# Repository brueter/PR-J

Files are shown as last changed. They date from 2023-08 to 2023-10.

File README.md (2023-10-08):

<p align="center">
    <picture>
        <source media="(prefers-color-scheme: dark)" srcset="./images/dark.svg" | width=300>
        <source media="(prefers-color-scheme: light)" srcset="./images/light.svg" | width=300>
        sammich
    </picture>
</p>

## PR and what now?
PR&J is the second name of this project after realizing two things:
- I'd like to be able to put this on a resume.
- Realizing the main features are as follows:
    - Probing
    - Runout detection
    - & Jam detection
> This board also is sandwiched between the hotend and extruder, thus a PR&J.

> If you'd like to know the first name of the board scroll up a bit in the discord

## How does a load cell do all that?
The way this design is set to work is there will be a strain gauge between the extruder and hotend with a set of resistors on it.
When the board experiences even the slightest bit of strain, the value of these resistors changes slightly.
This change is amplified by the tried and true HX717 24 bit amplifier, allowing for over 16 million unique values.
This signal is then read by an on board ATTiny202, and then sent to a klipper MCU via I<sub>2</sub>C.

Though the first idea that comes to mind with load cells is probing (which is still the main feature of this project), the ability to detect this strain can also be used to interpret forces between the hotend and extruder in both positive and negative directions.
We're still workshopping ideas that could come from this one feature, but some we would like to consider are:
- Runout detection
- Jam detection
- Detecting skipped steps
- One-click pressure advance tuning
- One-click max flow rate calculation

Some "theoreticals" that will need extensive testing but may be possible:
- Spaghetti detection
- Crash detection
- Flow rate change compensation

## Sign me up!
Actually I'd love to!
We're in the process of establishing a small beta test group for main boards and two types of strain gauges. The initial testing phase likely won't involve much printing, focusing instead on gathering data to study the behavior of these strain gauges, as well as test consistency.
As we develop more, the strain gauges we currently have may be adapted to some toolheads, so it's likely that new hardware won't even have to be sent for real world testing.
We're also looking for people that may have experience with any of the following for helping with development of the project itself.
- Skilled programmers, especially those familiar with klipper
- Electronics engineers
- CAD experts
If you're interested in contributing, ongoing discussions are hosted on the [Armchair Engineering discord server](https://discord.gg/armchairengineeringsux) in [this specific channel](https://discord.com/channels/1029426383614648421/1141480604844703745).

## What now?
As of the repository's creation, parts are on the way, and the board ordering process is nearly finalized. The initial batch of test boards will comprise approximately 10 main boards and 20 strain gauges (10 of each design).
Regular updates will be posted in the Armchair engineering project thread. Feel free to reach out to me there or through [my discord](https://discord.com/users/96435324275658752) if you have any questions.

Here's what we've got so far :)

<picture>
  <source srcset="./images/boards.png">
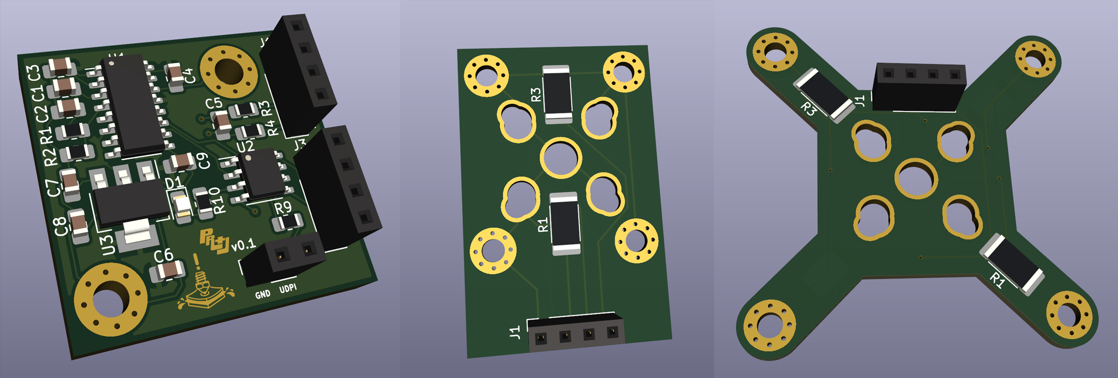
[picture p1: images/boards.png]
sammich
  
</picture>

## Helpers
- Electronics
    - [fisheiyy](https://github.com/fisheiyy)
    - [tanaes](https://github.com/tanaes)
    - [calithameridi](http://github.com/calithameridi/)
- Hardware
    - [tanaes](https://github.com/tanaes)
    - [bwnance](https://github.com/bwnance)
- Software
    - [detunedcalliope](https://github.com/detunedcalliope)

## Legal

Shield: [][cc-by-nc-sa]

This work is licensed under a
[Creative Commons Attribution-NonCommercial-ShareAlike 4.0 International License][cc-by-nc-sa].

[][cc-by-nc-sa]

[cc-by-nc-sa]: http://creativecommons.org/licenses/by-nc-sa/4.0/
[cc-by-nc-sa-image]: https://licensebuttons.net/l/by-nc-sa/4.0/88x31.png
[cc-by-nc-sa-shield]: https://img.shields.io/badge/License-CC%20BY--NC--SA%204.0-lightgrey.svg

FOR COMMERCIAL RIGHTS CONTACT AT brueter918@gmail.com

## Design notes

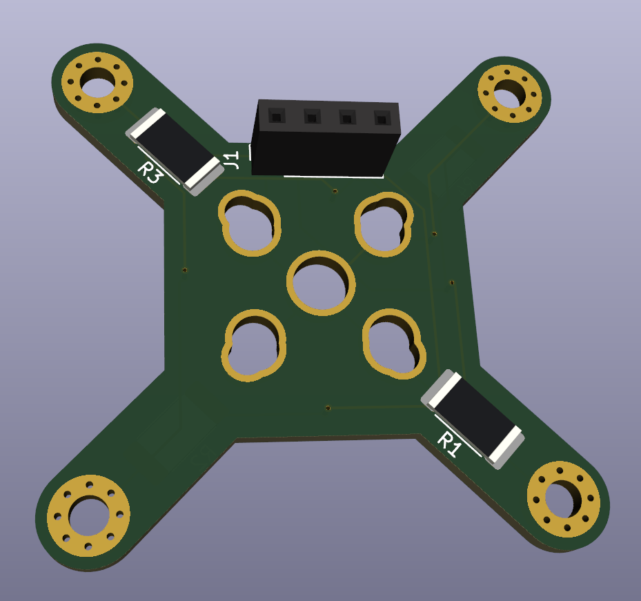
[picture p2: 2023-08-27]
images/square strain gauge.png

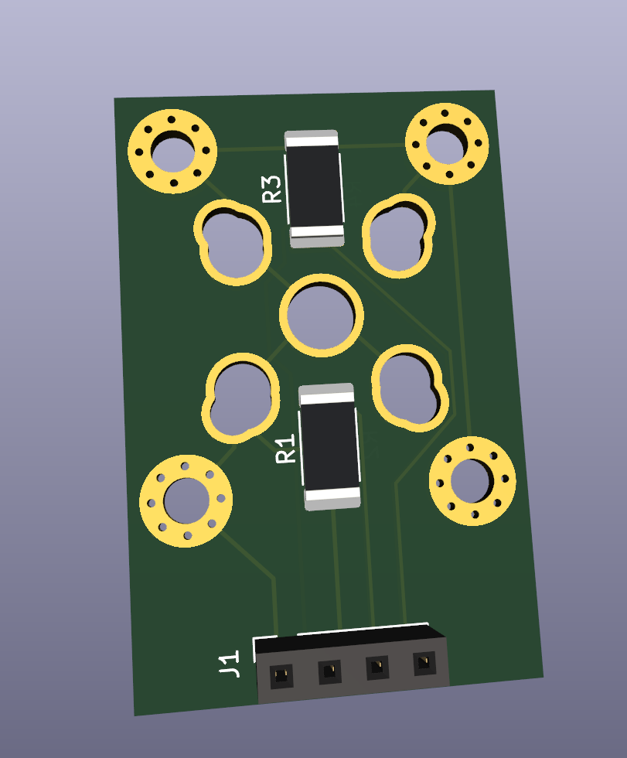
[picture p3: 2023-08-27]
images/minimal strain gauge.png

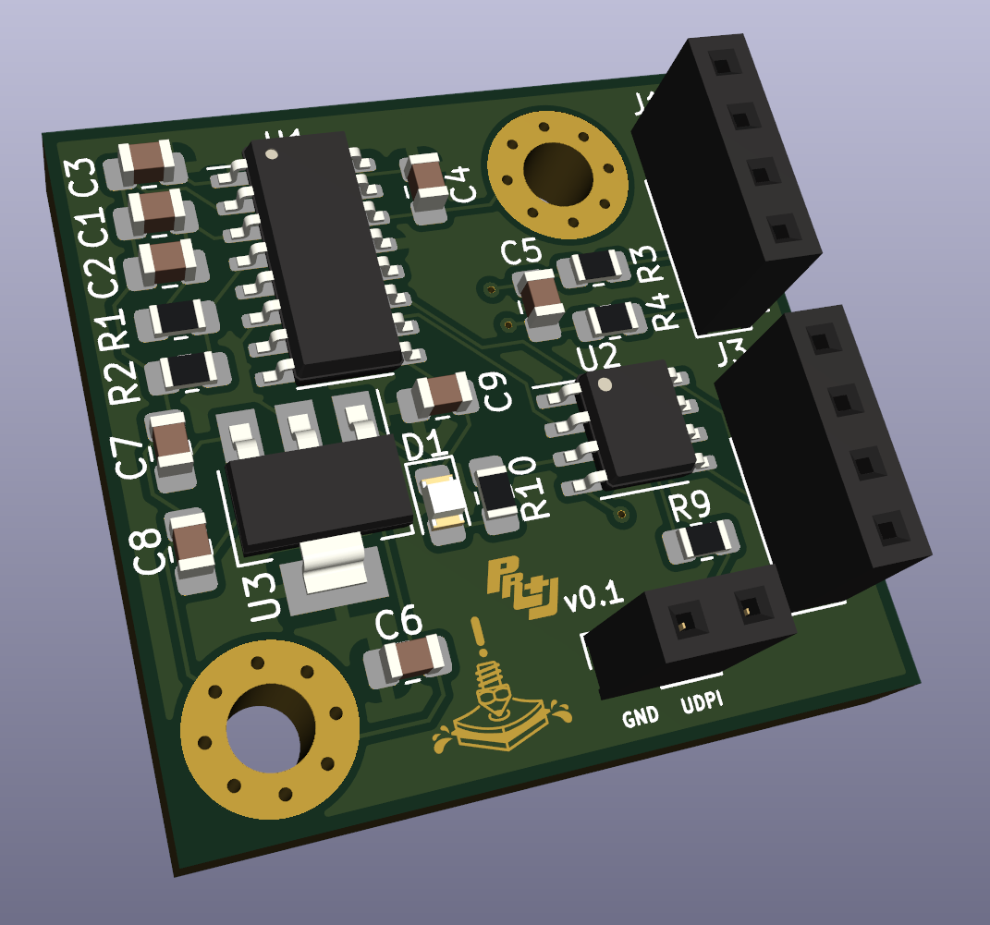
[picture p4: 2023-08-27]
images/driver board.png

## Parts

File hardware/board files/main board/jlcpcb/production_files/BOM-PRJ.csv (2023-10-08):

Comment | Designator | Footprint | LCSC
100 | R3 | R_0805_2012Metric_Pad1.20x1.40mm_HandSolder
10u | C7 | C_0805_2012Metric_Pad1.18x1.45mm_HandSolder
Strain Gauge | J1 | PinSocket_1x04_P2.54mm_Vertical
4k7 | R9 | R_0805_2012Metric_Pad1.20x1.40mm_HandSolder
MountingHole_Pad | H1 | MountingHole_3.2mm_M3_Pad_Via
12K | R2 | R_0805_2012Metric_Pad1.20x1.40mm_HandSolder
10u | C4 | C_0805_2012Metric_Pad1.18x1.45mm_HandSolder
HX717 | U1 | SOP-16_3.9x9.9mm_P1.27mm
10u | C9 | C_0805_2012Metric_Pad1.18x1.45mm_HandSolder
10u | C2 | C_0805_2012Metric_Pad1.18x1.45mm_HandSolder
Programmer | J2 | PinSocket_1x02_P2.54mm_Vertical
AMS1117-3.3 | U3 | SOT-223-3_TabPin2
ATtiny202-SS | U2 | SOIC-8_3.9x4.9mm_P1.27mm
KLIPPER | J3 | PinSocket_1x04_P2.54mm_Vertical
0u1 | C3 | C_0805_2012Metric_Pad1.18x1.45mm_HandSolder
100 | R4 | R_0805_2012Metric_Pad1.20x1.40mm_HandSolder
MountingHole_Pad | H2 | MountingHole_3.2mm_M3_Pad_Via
10u | C8 | C_0805_2012Metric_Pad1.18x1.45mm_HandSolder
0u1 | C5 | C_0805_2012Metric_Pad1.18x1.45mm_HandSolder
0u1 | C1 | C_0805_2012Metric_Pad1.18x1.45mm_HandSolder
100 | R10 | R_0805_2012Metric_Pad1.20x1.40mm_HandSolder
B1701NB | D1 | LED_0805_2012Metric_Pad1.15x1.40mm_HandSolder
0u1 | C6 | C_0805_2012Metric_Pad1.18x1.45mm_HandSolder
33K | R1 | R_0805_2012Metric_Pad1.20x1.40mm_HandSolder

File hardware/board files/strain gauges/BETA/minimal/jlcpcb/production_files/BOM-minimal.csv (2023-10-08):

Comment | Designator | Footprint | LCSC
PR&J | J1 | PinSocket_1x04_P2.54mm_Vertical
1k | R3 | R_2512_6332Metric
MountingHole_Pad | H1 | MountingHole_3.2mm_M3_Pad_Via
~ | U1 | hotend mounting holes
MountingHole_Pad | H2 | MountingHole_3.2mm_M3_Pad_Via
1k | R1 | R_2512_6332Metric
MountingHole_Pad | H3 | MountingHole_3.2mm_M3_Pad_Via
MountingHole_Pad | H4 | MountingHole_3.2mm_M3_Pad_Via
1k | R2 | R_2512_6332Metric
1k | R4 | R_2512_6332Metric

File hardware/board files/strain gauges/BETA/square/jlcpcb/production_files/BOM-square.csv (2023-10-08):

Comment | Designator | Footprint | LCSC
1k | R3 | R_2512_6332Metric_Pad1.40x3.35mm_HandSolder
1k | R1 | R_2512_6332Metric_Pad1.40x3.35mm_HandSolder
1k | R2 | R_2512_6332Metric_Pad1.40x3.35mm_HandSolder
1k | R4 | R_2512_6332Metric_Pad1.40x3.35mm_HandSolder

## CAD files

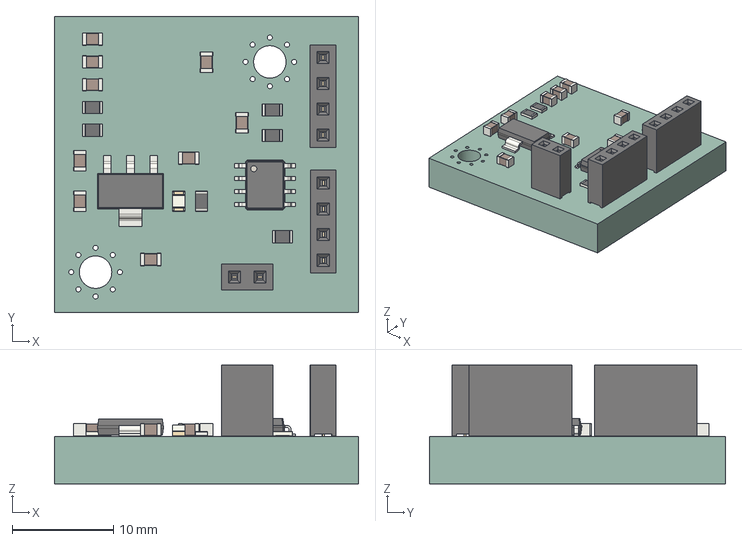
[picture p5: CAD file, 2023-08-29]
hardware/board files/main board/PRJ.step
30.0 x 29.2 x 11.7 mm
PRJ PCB

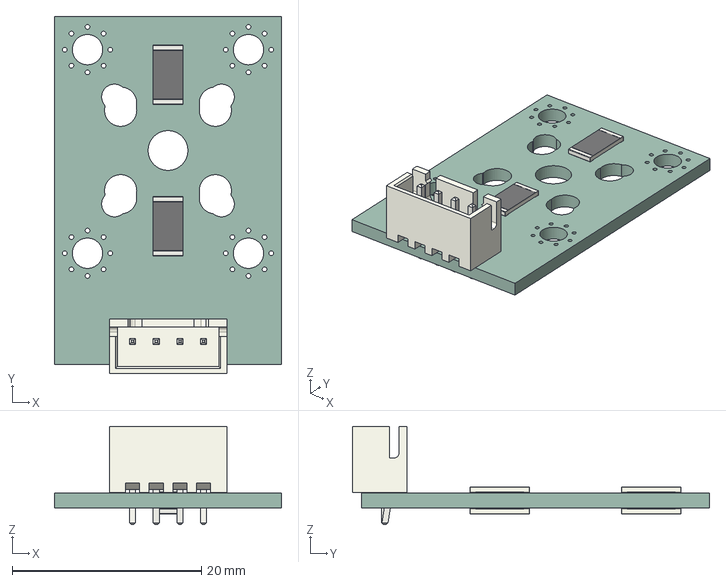
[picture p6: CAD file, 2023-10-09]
hardware/board files/strain gauges/BETA/minimal/strain gauge.step
24.0 x 37.7 x 10.4 mm
minimal PCB

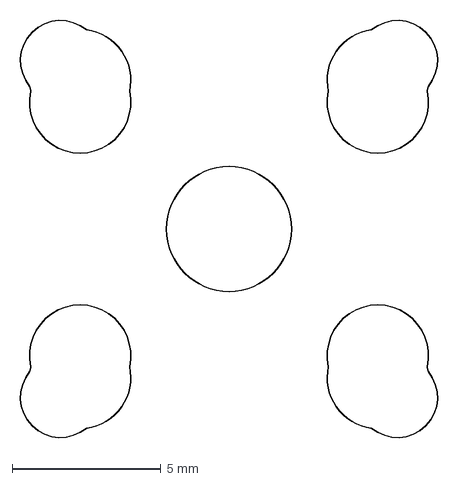
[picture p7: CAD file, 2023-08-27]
hardware/board files/strain gauges/hotend mounting holes.dxf
14.3 x 14.3 mm

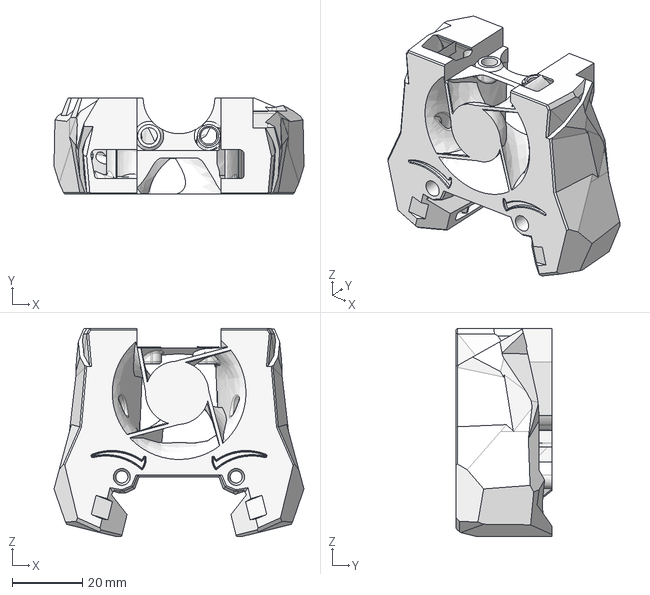
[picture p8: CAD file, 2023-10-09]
hardware/toolhead/cad/stealthjelly front.step
71.1 x 27.4 x 59.1 mm

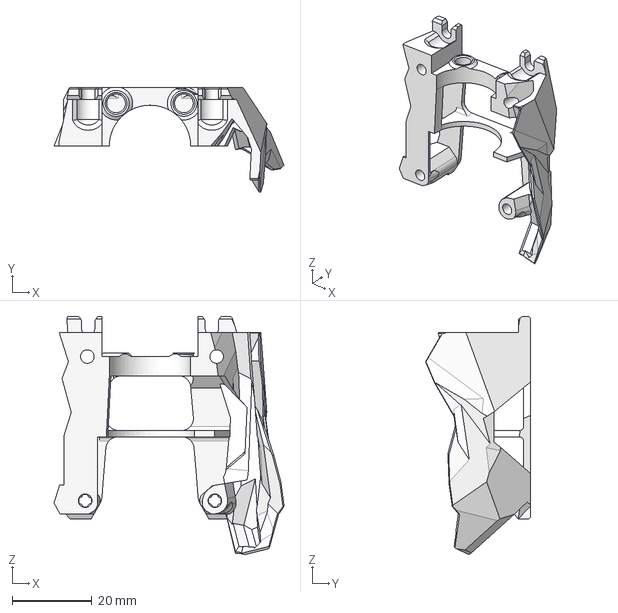
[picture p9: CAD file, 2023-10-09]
hardware/toolhead/cad/stealthjelly back.step
57.7 x 26.3 x 59.7 mm

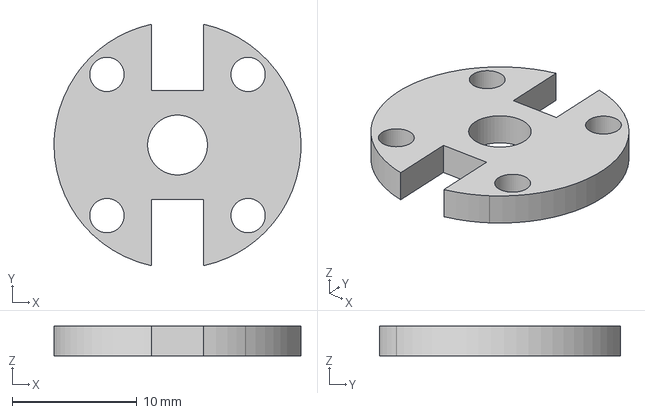
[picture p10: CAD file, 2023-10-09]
hardware/toolhead/cad/spacer.step
19.8 x 19.3 x 2.40 mm

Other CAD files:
hardware/toolhead/stl/spacer.stl
hardware/toolhead/stl/stealthjelly back.stl

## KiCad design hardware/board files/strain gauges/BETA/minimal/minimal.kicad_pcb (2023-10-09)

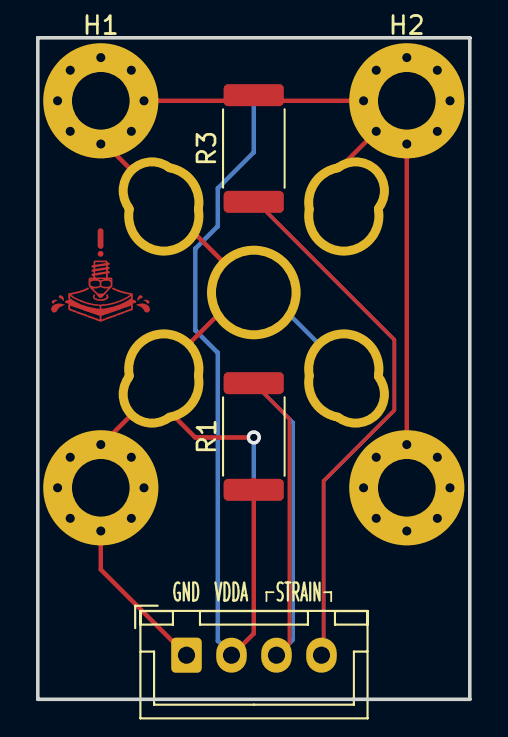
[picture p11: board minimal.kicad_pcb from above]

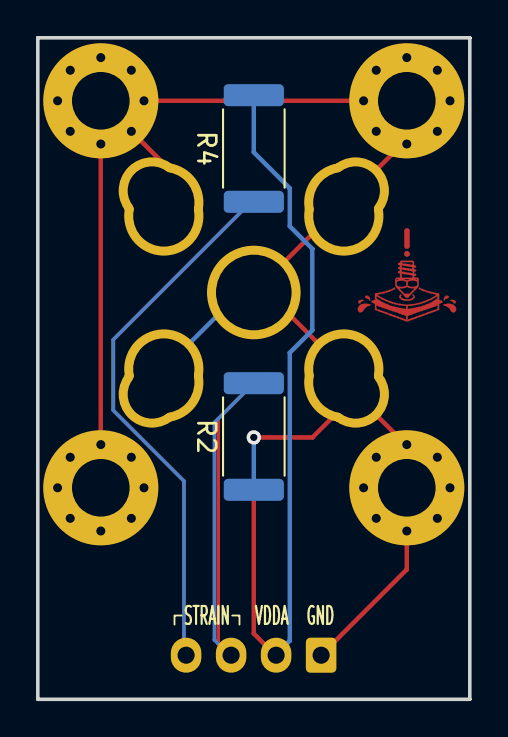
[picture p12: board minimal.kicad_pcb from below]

Board: 2 copper layers, 24.0 x 36.8 mm, 10 parts (2 on the bottom side), 4 nets.

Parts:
H1, H2, H3, H4: MountingHole_Pad; MountingHole_3.2mm_M3_Pad_Via
J1: PR&J; JST_XH_B4B-XH-A_1x04_P2.50mm_Vertical
R1, R2, R3, R4: 1k; R_2512_6332Metric
U1: hotend mounting holes

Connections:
GND: H1.1, H2.1, H3.1, H4.1, J1.1, R2.1, R3.2, U1.1 (GND)
IN+: J1.3, R1.2, R2.2
IN-: J1.4, R3.1, R4.1
VDDA: J1.2, R1.1, R4.2

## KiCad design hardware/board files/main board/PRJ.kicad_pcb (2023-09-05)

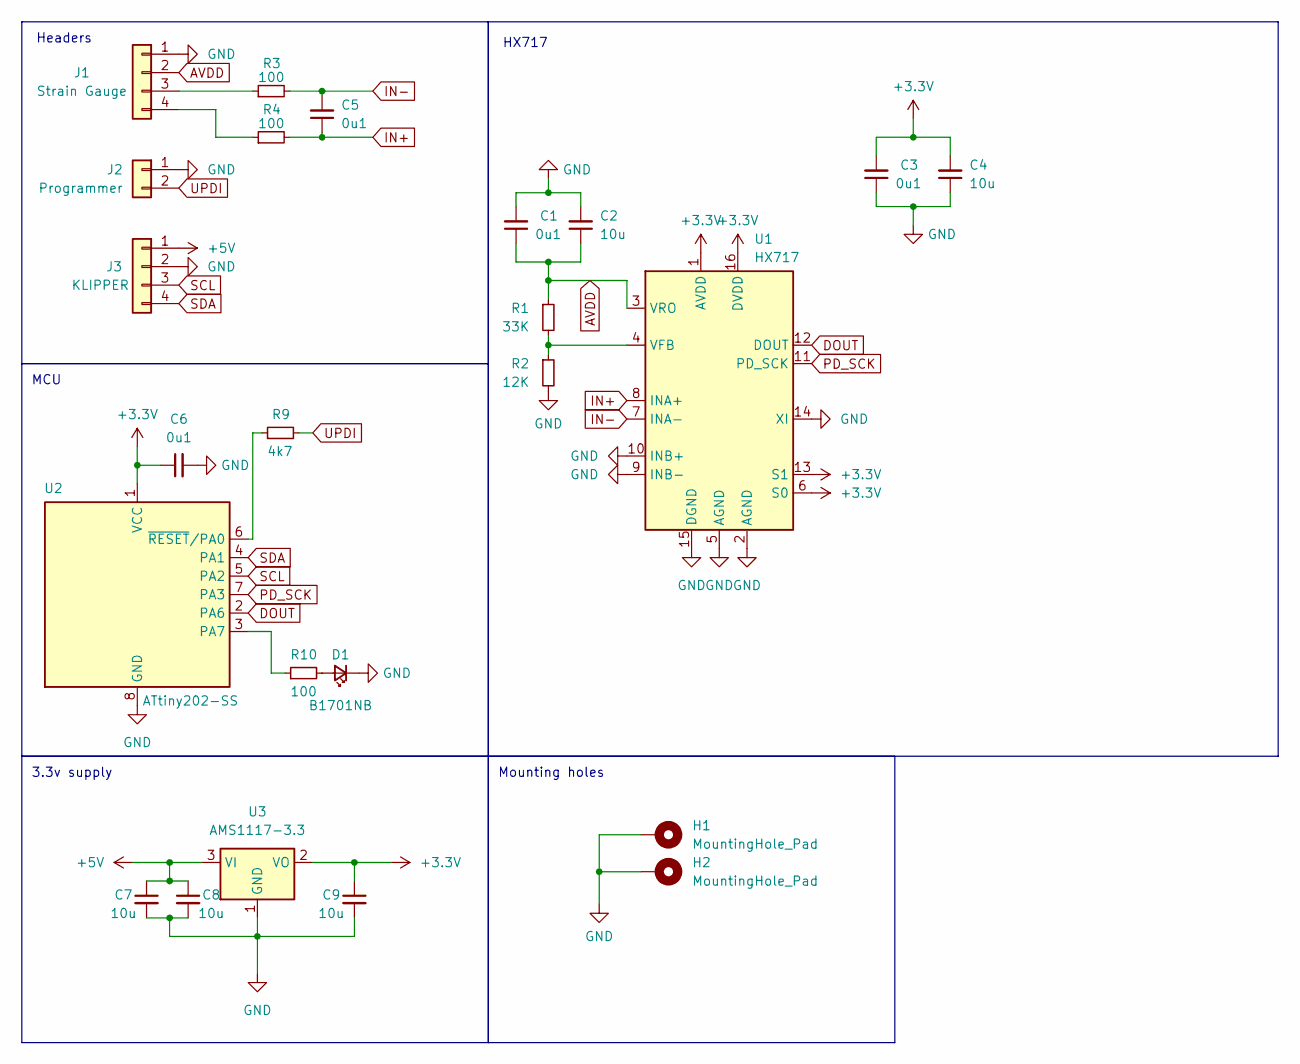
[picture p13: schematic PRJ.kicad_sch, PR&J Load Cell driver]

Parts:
C1, C3, C5, C6: 0u1; C_0805_2012Metric_Pad1.18x1.45mm_HandSolder
C2, C4, C7, C8, C9: 10u; C_0805_2012Metric_Pad1.18x1.45mm_HandSolder
D1: B1701NB; LED_0805_2012Metric_Pad1.15x1.40mm_HandSolder
H1, H2: MountingHole_Pad; MountingHole_3.2mm_M3_Pad_Via
J1: Strain Gauge; PinSocket_1x04_P2.54mm_Vertical
J2: Programmer; PinSocket_1x02_P2.54mm_Vertical
J3: KLIPPER; PinSocket_1x04_P2.54mm_Vertical
R1: 33K; R_0805_2012Metric_Pad1.20x1.40mm_HandSolder
R2: 12K; R_0805_2012Metric_Pad1.20x1.40mm_HandSolder
R3, R4, R10: 100; R_0805_2012Metric_Pad1.20x1.40mm_HandSolder
R9: 4k7; R_0805_2012Metric_Pad1.20x1.40mm_HandSolder
U1: HX717; SOP-16_3.9x9.9mm_P1.27mm
U2: ATtiny202-SS; SOIC-8_3.9x4.9mm_P1.27mm
U3: AMS1117-3.3; SOT-223-3_TabPin2

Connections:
+3.3V: C3.2, C4.2, C6.1, C9.1, U1.1 (AVDD), U1.6 (S0), U1.13 (S1), U1.16 (DVDD), U2.1 (VCC), U3.2 (VO)
+5V: C7.1, C8.1, J3.1, U3.3 (VI)
AVDD: C1.1, C2.1, J1.2, R1.1, U1.3 (VRO)
DOUT: U1.12 (DOUT), U2.2 (PA6)
GND: C1.2, C2.2, C3.1, C4.1, C6.2, C7.2, C8.2, C9.2, D1.1 (K), H1.1, H2.1, J1.1, J2.1, J3.2, R2.2, U1.2 (AGND), U1.5 (AGND), U1.9 (INB-), U1.10 (INB+), U1.14 (XI), U1.15 (DGND), U2.8 (GND), U3.1 (GND)
IN+: C5.1, R4.2, U1.8 (INA+)
IN-: C5.2, R3.2, U1.7 (INA-)
unnamed: D1.2 (A), R10.2
unnamed: J1.3, R3.1
unnamed: J1.4, R4.1
unnamed: R1.2, R2.1, U1.4 (VFB)
unnamed: R10.1, U2.3 (PA7)
unnamed: R9.1, U2.6 (~RESET/PA0)
PD_SCK: U1.11 (PD_SCK), U2.7 (PA3)
SCL: J3.3, U2.5 (PA2)
SDA: J3.4, U2.4 (PA1)
UPDI: J2.2, R9.2

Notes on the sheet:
Headers
HX717
Mounting holes
3.3v supply
MCU

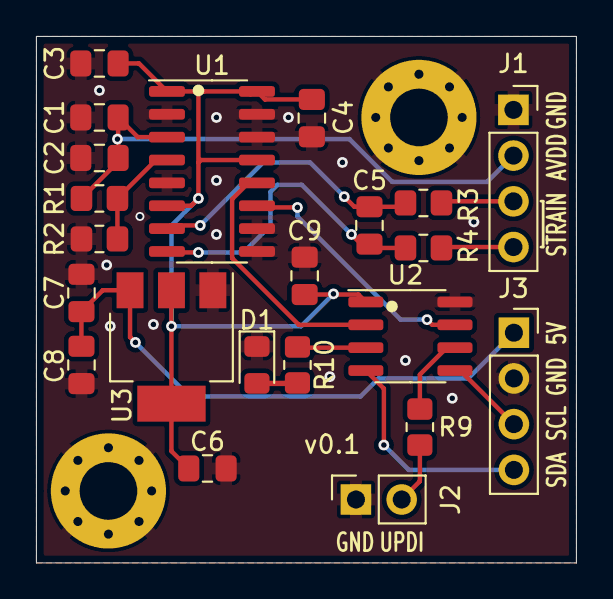
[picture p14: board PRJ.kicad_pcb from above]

Board: 2 copper layers, 30.0 x 29.2 mm, 24 parts (0 on the bottom side), 17 nets.

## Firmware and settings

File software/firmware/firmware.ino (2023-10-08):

#include <Wire.h>

const byte DOUT = 0;
const byte CLK = 4;
const byte LED = 1;
const int MEDIAN_FILTER_SIZE = 3; // Adjust this value based on your requirements
const int LOW_PASS_FILTER_SIZE = 10;

void setup() {
  Wire.begin(8);
  Wire.onRequest(rx);
  pinMode(DOUT, INPUT_PULLUP);
  pinMode(CLK, OUTPUT);
  pinMode(LED, OUTPUT);
}

void loop() {
  
}

inline void rx(void) {
  unsigned long smoothedValue = readAndFilter();
  byte longBytes[4];
  memcpy(longBytes, &smoothedValue, 4);
  Wire.write(longBytes, 4);
}

unsigned long readAndFilter() {
  unsigned long buffer[MEDIAN_FILTER_SIZE];
  
  for (int i = 0; i < MEDIAN_FILTER_SIZE; i++) {
    buffer[i] = read();
  }

  unsigned long median = calculateMedian(buffer, MEDIAN_FILTER_SIZE);

  static unsigned long filterBuffer[LOW_PASS_FILTER_SIZE];
  static int index = 0;
  static unsigned long sum = 0;
  
  filterBuffer[index] = median;
  sum += filterBuffer[index] - filterBuffer[(index + 1) % LOW_PASS_FILTER_SIZE];
  index = (index + 1) % LOW_PASS_FILTER_SIZE;
  
  return sum / LOW_PASS_FILTER_SIZE;
}

unsigned long read() {
  unsigned long output = 0;
  byte i;

  digitalWrite(CLK, LOW);
  
  while (digitalRead(DOUT) == HIGH);

  for (i = 0; i < 24; i++) {
    digitalWrite(CLK, HIGH);
    output = output << 1;
    digitalWrite(CLK, LOW);
    if (digitalRead(DOUT)) output++;
  }

  digitalWrite(CLK, HIGH);
  output = output ^ 0x800000;
  digitalWrite(CLK, LOW);
  
  return output;
}

unsigned long calculateMedian(unsigned long* values, int length) {
  // Sort the array to find the median
  for (int i = 0; i < length - 1; i++) {
    for (int j = i + 1; j < length; j++) {
      if (values[i] > values[j]) {
        unsigned long temp = values[i];
        values[i] = values[j];
        values[j] = temp;
      }
    }
  }

  // The median is at the middle of the sorted array
  return values[length / 2];
}

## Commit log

2023-08-27 initial commit, contains board files
    [PRJ.kicad_pcb, PRJ.kicad_sch, hotend mounting holes.dxf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]
2023-08-27 fixed strain gauge routing, added images of all boards
    [minimal.kicad_pcb]
2023-08-27 moved images of boards
2023-08-27 added PRJ logo to strain gauge boards
    [square.kicad_pcb]
2023-08-29 first revision of on board firmware, separate hardware and software folders
    [PRJ.kicad_pcb, PRJ.kicad_sch, PRJ.step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]
2023-09-04 overhauled main board, updated credits
    [PRJ.kicad_pcb, PRJ.kicad_sch]
2023-09-04 adjusted mainboard
    [PRJ.kicad_pcb]
2023-09-05 finalized boards for production
    [PRJ.kicad_pcb, minimal.kicad_pcb]
2023-10-08 updated 202 firmware to add software low pass filtering and median filtering
    [BOM-PRJ.csv, BOM-minimal.csv, BOM-square.csv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]
2023-10-09 added cad and stl files for initial test version of a modified stealthburner, currently being reffered to as stealthjelly
    [minimal.kicad_pcb, minimal.kicad_sch, spacer.step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]
2023-10-09 fixed issue with front part
    [stealthjelly front.step]
2023-10-09 fixed heat sets being too small on front
    [stealthjelly back.step, stealthjelly back.stl, stealthjelly front.step]
2023-10-11 added software to analyze data from an excel spreadsheet alongside various filtering methods
    [data.xlsx]

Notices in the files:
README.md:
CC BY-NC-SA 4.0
